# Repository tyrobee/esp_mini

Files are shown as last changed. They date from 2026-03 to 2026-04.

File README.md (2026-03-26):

# esp_mini
A Esp  based flight controller which is really tiny and can be controller through almost everything from your phone to anthor esp and cn also be used as swarn drones likw the drones which do all those cool drone lighting show. Actually i made this drone with that idea only ive been seen those swarn drones show in my school and wated to do smtg like that but there not a single affordable platform for that but you can achevie the same results with this drone at a really affordable range.

## compnents 
- Xiao ESP32 S3 (FC)
- MPU 6050
- 8520 Coreless Motor 2xCW & 2xCCW
- 55mm Propeller 2xCW & 2xCCW
- Coustom motor drive:
    • SI2300 1N-MOSFET 4x
    • 1N4148 Diode 4x
    • 10k ohm Resistor 4X
## Frame
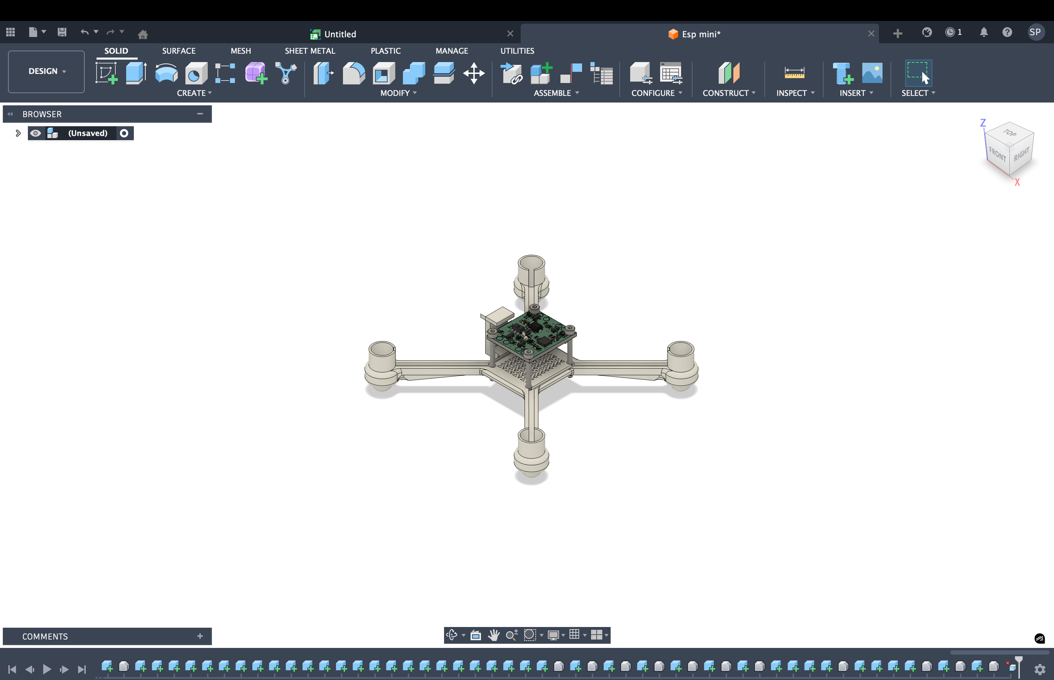
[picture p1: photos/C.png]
C


# Schematics
 Here is the break down of the connections 
  MOTORS-
  M1 --> A8
  M2 --> A3
  M3 --> A2
  M4 --> A0

  MPU6050-
  SDA --> A4
  SCL --> A5

  CRSF- (you can change this part but as i have a csrf radio i have done it for a csrf receiver)
  RX --> D7
  TX --> D6

  3.7v to 5v-
  for reciver to get powered 

  led-
  2 power led
  1 arm led

  Battery Voltage Telemetry-
  Vin --> A1

# PCB 
The PCB is designed in Kicad 
top -
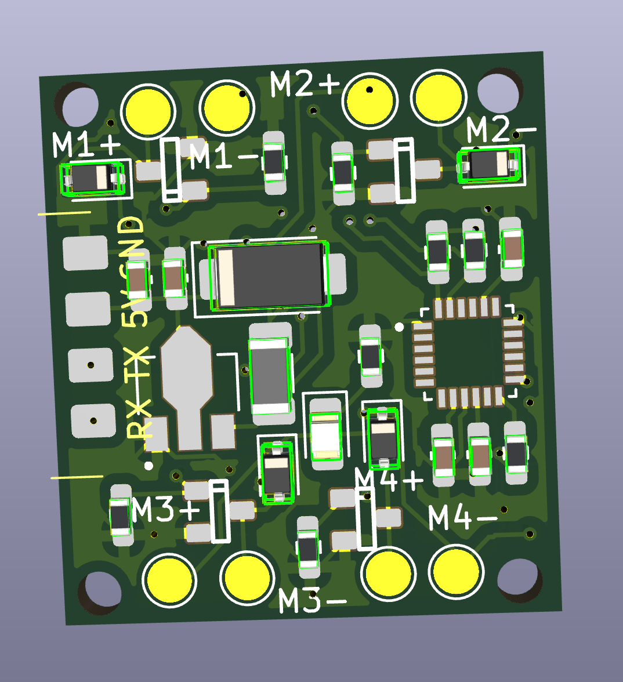
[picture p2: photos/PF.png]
PF


bottom -
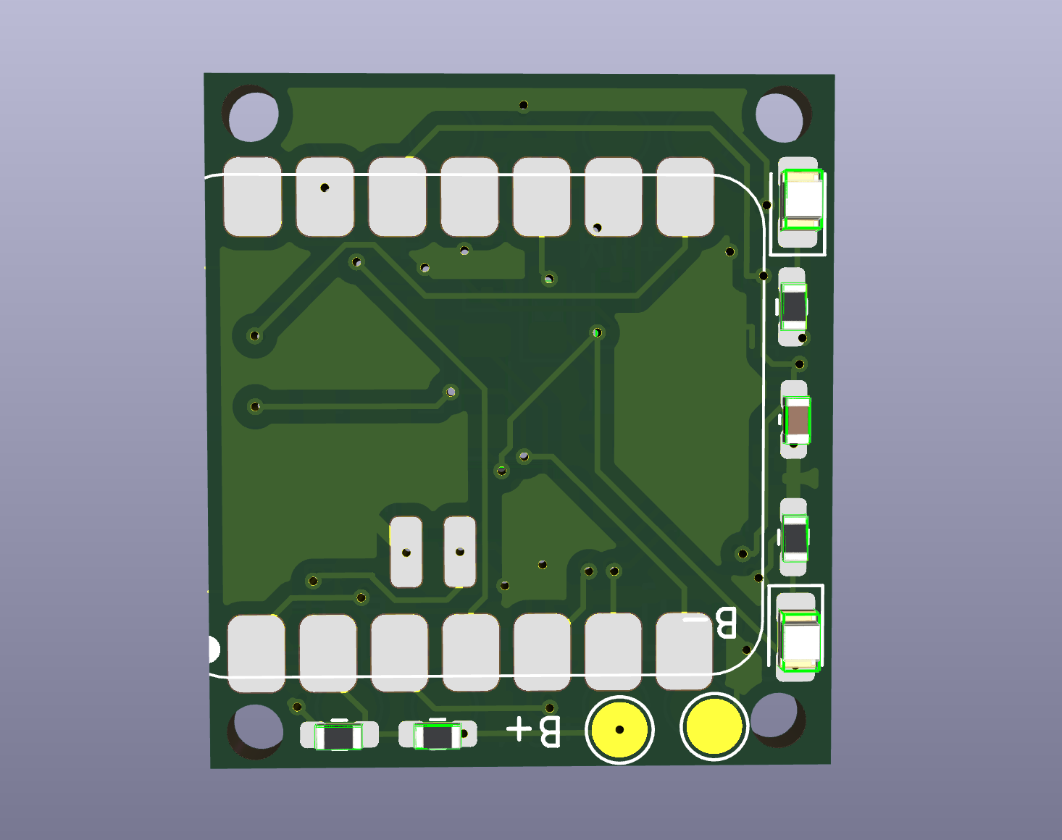
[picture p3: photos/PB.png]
PB


# Firmware

This project uses open-source flight controller firmware from the ESP-FC project,
developed by rtlopez.

- Original firmware repository:
  https://github.com/rtlopez/esp-fc

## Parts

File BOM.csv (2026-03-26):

Item | Description | Quantity | Unit Price($) | Total Price($) | URL
XIAO ESP32 S3 | Flight Controller | 1 | 8.82 | 8.82 | https://robocraze.com/products/seeed-studio-xiao-esp32-s3-development-board-supports-wi-fi-bluetooth-5-0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
8520 Coreless Brushed Motor | Motors | 1 set(4Pcs) | 6.45 | 6.45 | https://roboticsdna.in/product/coreless-motors-720-series-45000-rpm-3-7v/
55 mm Blade Propeller | Propeller | 1set(4Pcs) | 0.56 | 0.56 | https://roboticsdna.in/product/4pcs-set-55mm-white-propeller-for-h107l-h107c-h107d（aperture-1mm）/
1N SI2300 MOSFET | To drive motor | 4 | 0.046 | 0.19 | https://robu.in/product/si2300-hxy-mosfet-20v-6a-350mw-27mω4-5v-500mv-1-n-channel-sot-23-mosfets-rohs/
1N4148 SMD | Diode | 4 | 0.026 | 0.10 | https://robu.in/product/ac1206fr-0710kl-yageo-res-thick-film-1206-10k-ohm-1-0-25w1-4w-±100ppm-c-pad-smd-t-r-automotive-aec-q200/
10k ohm SMD | Resister | 5 | 0.0052 | 0.0262
1k ohm SMD | Resister | 4 | 0.0030 | 0.012
150 ohm SMD | Resister | 3 | 0.0011 | 0.0033
0.01uF SMD | Capacitor | 4 | 0.0030 | 0.012
LED 0805 SMD | Led | 3 | 0.029 | 0.097
ME2108A33P Module | Boost converter | 1 | 0.57 | 0.57 | https://www.flyrobo.in/1.5v-1.8v-2.5v-3v-3.3v-3.7v-4.2v-5v-dc-dc-dc-boost-converter-step-up-module
MPU6050 | Gyro and accelerometer | 1 | 1.91 | 1.91 | https://robu.in/product/mpu-6050-gyro-sensor-2-accelerometer/
1S 300mah battery | Battery | 1 | 1.92 | 1.92 | https://robu.in/product/wly702025-300mah-3-7v-single-cell-rechargeable-lipo-battery/
RadioMaster XR2 Nano | ELRS recover | 1 | 12.12 | 12.12 | https://rcmumbai.com/products/radiomaster-xr2-nano-2-4ghz-expresslrs-receiver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
PCB | Pcb | 5 | 4.9 | 4.9 | SeedStudio
Frame | 3d printing | 1 | 6.4 | 0.9 | 3D
 |  |  | Shipment | 4.56+ 1.66+0.76+0.54+0.65+0.54+1.66 =10.28
 |  |  | Tax(3Dprint & Motors |  | 2.52
 |  |  | Total= | 51.38 ~ 51.5

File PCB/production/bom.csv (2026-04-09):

Designator | Footprint | Quantity | Value | LCSC Part #
B+ | TestPoint_Pad_D2.0mm | 1 | B+
B- | TestPoint_Pad_D2.0mm | 1 | B-
C1, C2, C3, C4 | 0603 | 4 | 0.01uF
C5, C6 | 0603 | 2 | 12uF
D1, D2, D3, D4 | D_SOD-323 | 4 | 1N4148WS
D10 | D_SMA | 1 | SS14
D5, D6, D7 | 0805 | 3 | LED
L1 | 1206 | 1 | 22uH
M1, M2, M3, M4 | SOT23_1_ | 4 | SI2300
M1+ | TestPoint_Pad_D2.0mm | 1 | m1-
M1- | TestPoint_Pad_D2.0mm | 1 | m1+
M2+ | TestPoint_Pad_D2.0mm | 1 | m2+
M2- | TestPoint_Pad_D2.0mm | 1 | m2-
M3+ | TestPoint_Pad_D2.0mm | 1 | m3+
M3- | TestPoint_Pad_D2.0mm | 1 | m3-
M4+ | TestPoint_Pad_D2.0mm | 1 | m4-
M4- | TestPoint_Pad_D2.0mm | 1 | m4+
PS1 | CONV_ME2108A33P | 1 | ME2108A33P
R1, R2, R3, R4 | 0603 | 4 | 1k
R10, R5, R6, R7, R8 | 0603 | 5 | 10k
R11, R12, R9 | 0603 | 3 | 150
U10 | XIAO-ESP32-S3-SMD_PAD | 1 | XIAO-ESP32-S3-SMD
U11 | XR2 NANO | 1 | ~
U3 | QFN50P400X400X95-24N | 1 | MPU-6050

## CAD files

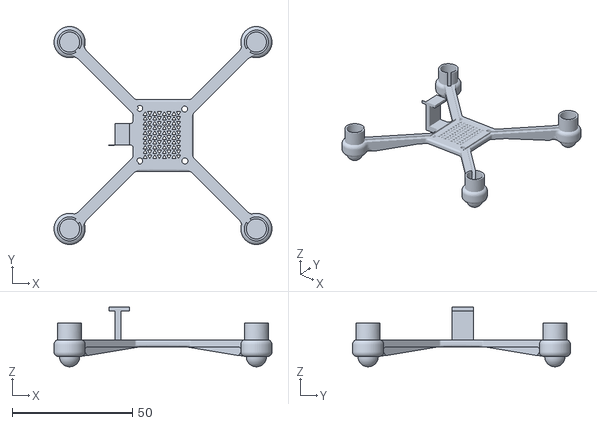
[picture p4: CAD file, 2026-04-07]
esp mini.stl
90.8 x 90.8 x 24.8

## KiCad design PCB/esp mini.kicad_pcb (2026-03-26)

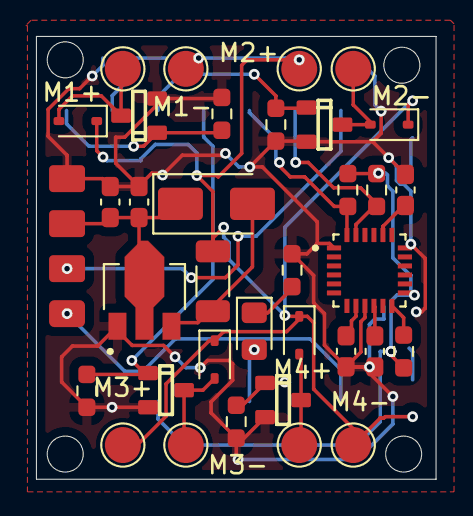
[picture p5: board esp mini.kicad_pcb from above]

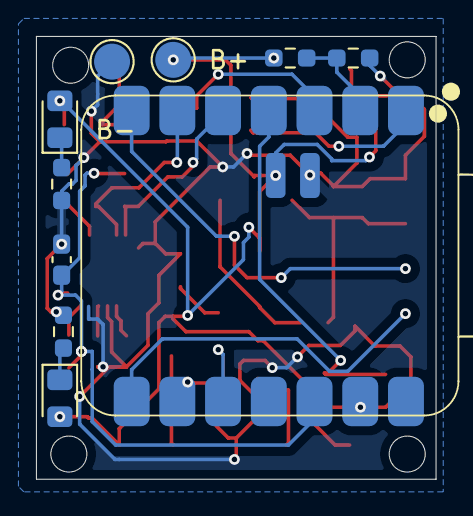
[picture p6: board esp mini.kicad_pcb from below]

Board: 2 copper layers, 22.2 x 24.6 mm, 45 parts (10 on the bottom side), 26 nets.

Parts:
B+: B+; TestPoint_Pad_D2.0mm
B-: B-; TestPoint_Pad_D2.0mm
C1, C2, C3, C4: 0.01uF; C_0603_1608Metric_Pad1.08x0.95mm_HandSolder
C5, C6: 12uF; C_0603_1608Metric_Pad1.08x0.95mm_HandSolder
D1, D2, D3, D4: 1N4148WS; D_SOD-323
D5, D6, D7: LED; LED_0805_2012Metric_Pad1.15x1.40mm_HandSolder
D10: SS14; D_SMA
L1: 22uH; L_1206_3216Metric_Pad1.22x1.90mm_HandSolder
M1, M2, M3, M4: SI2300; SOT23_1_
M1+: m1-; TestPoint_Pad_D2.0mm
M1-: m1+; TestPoint_Pad_D2.0mm
M2+: m2+; TestPoint_Pad_D2.0mm
M2-: m2-; TestPoint_Pad_D2.0mm
M3+: m3+; TestPoint_Pad_D2.0mm
M3-: m3-; TestPoint_Pad_D2.0mm
M4+: m4-; TestPoint_Pad_D2.0mm
M4-: m4+; TestPoint_Pad_D2.0mm
PS1: ME2108A33P; CONV_ME2108A33P
R1, R2, R3, R4: 1k; R_0603_1608Metric_Pad0.98x0.95mm_HandSolder
R5, R6, R7, R8, R10: 10k; R_0603_1608Metric_Pad0.98x0.95mm_HandSolder
R9, R11, R12: 150; R_0603_1608Metric_Pad0.98x0.95mm_HandSolder
U3: MPU-6050; QFN50P400X400X95-24N
U10: XIAO-ESP32-S3-SMD; XIAO-ESP32-S3-SMD_PAD
U11: XR2 NANO

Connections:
+3.3V: C4.1, R5.1, R6.1, R7.1, U3.13 (VDD), U10.12 (3V3)
+3.3VA: B+.1, D1.1 (K), D2.1 (K), D3.1 (K), D4.1 (K), D6.2 (A), D7.2 (A), L1.1, M1-.1, M2+.1, M3+.1, M4-.1, R8.1, U10.15 (BAT)
+5V: C5.1, C6.1, D10.1 (K), PS1.2 (VOUT), U11.3 (5V)
/LBAT: D5.2 (A), U10.10 (PA5_A9_D9_MISO)
/M1: M1.1, R1.2, U10.1 (PA02_A0_D0)
/M2: M2.1, R2.2, U10.3 (PA10_A2_D2)
/M3: M3.1, R3.2, U10.4 (PA11_A3_D3)
/M4: M4.1, R4.2, U10.9 (PA7_A8_D8_SCK)
/RX: U10.8 (PB09_A7_D7_RX), U11.1 (RX)
/SCL: R6.2, U3.23 (SCL), U10.6 (PA9_A5_D5_SCL)
/SDA: R7.2, U3.24 (SDA), U10.5 (PA8_A4_D4_SDA)
/TX: U10.7 (PB08_A6_D6_TX), U11.2 (TX)
/VBAT: R8.2, R10.1, U10.2 (PA4_A1_D1)
/int: R5.2, U3.12 (INT)
GND: B-.1, C1.2, C2.2, C3.2, C4.2, C5.2, C6.2, M1.2, M2.2, M3.2, M4.2, PS1.1 (VSS), R1.1, R2.1, R3.1, R4.1, R9.1, R10.2, R11.2, R12.2, U3.1 (CLKIN), U3.9 (AD0), U3.11 (FSYNC), U3.18 (GND), U10.13 (GND), U10.16 (GND), U11.4 (GND)
unnamed: D1.2 (A), M1.3, M1+.1
unnamed: D2.2 (A), M2.3, M2-.1
unnamed: D3.2 (A), M3.3, M3-.1
unnamed: D4.2 (A), M4.3, M4+.1
unnamed: D5.1 (K), R9.2
unnamed: D6.1 (K), R11.1
unnamed: D7.1 (K), R12.1
unnamed: D10.2 (A), L1.2, PS1.3 (LX)
unnamed: C2.1, U3.20 (CPOUT)
unnamed: C3.1, U3.10 (REGOUT)
unnamed: C1.1, U3.8 (VLOGIC)

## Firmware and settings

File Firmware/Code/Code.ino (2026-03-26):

`#include <WiFi.h>
#include <esp_now.h>
#include <Wire.h>
#include <MPU6050.h>

MPU6050 mpu;


#define M1_PIN 0
#define M2_PIN 2
#define M3_PIN 3
#define M4_PIN 8


#define CH1 0
#define CH2 1
#define CH3 2
#define CH4 3

#define PWM_FREQ 25000
#define PWM_RES 8   


#define MOTOR_MIN 25     
#define MOTOR_MAX 240
#define MOTOR_ARM 15


float kp = 0.18;
float ki = 0.00;
float kd = 0.003;


typedef struct {
  int throttle;
  int roll;
  int pitch;
  int yaw;
  bool armed;
} ControlData;

ControlData rx;


float rollPID, pitchPID, yawPID;
float rollError, pitchError, yawError;
float lastRollErr, lastPitchErr, lastYawErr;


float gx, gy, gz;
unsigned long lastTime;

void onReceive(const esp_now_recv_info_t *info, const uint8_t *data, int len) {
  memcpy(&rx, data, sizeof(rx));
}

void setup() {
  Serial.begin(115200);

  WiFi.mode(WIFI_STA);
  esp_now_init();
  esp_now_register_recv_cb(onReceive);

  
  Wire.begin();
  mpu.initialize();
  mpu.setFullScaleGyroRange(MPU6050_GYRO_FS_1000);

  
  ledcSetup(CH1, PWM_FREQ, PWM_RES);
  ledcSetup(CH2, PWM_FREQ, PWM_RES);
  ledcSetup(CH3, PWM_FREQ, PWM_RES);
  ledcSetup(CH4, PWM_FREQ, PWM_RES);

  ledcAttachPin(M1_PIN, CH1);
  ledcAttachPin(M2_PIN, CH2);
  ledcAttachPin(M3_PIN, CH3);
  ledcAttachPin(M4_PIN, CH4);

  lastTime = micros();
}

void loop() {
  
  if (!rx.armed) {
    stopAllMotors();
    return;
  }


  float dt = (micros() - lastTime) / 1000000.0;
  lastTime = micros();

  
  mpu.getRotation(&gx, &gy, &gz);
  rollRate  = gx / 131.0;
  pitchRate = gy / 131.0;
  yawRate   = gz / 131.0;

  
  rollError  = rx.roll  - rollRate;
  pitchError = rx.pitch - pitchRate;
  yawError   = rx.yaw   - yawRate;

  rollPID  = kp * rollError  + kd * ((rollError  - lastRollErr)  / dt);
  pitchPID = kp * pitchError + kd * ((pitchError - lastPitchErr) / dt);
  yawPID   = kp * yawError   + kd * ((yawError   - lastYawErr)   / dt);

  lastRollErr  = rollError;
  lastPitchErr = pitchError;
  lastYawErr   = yawError;

  int base = map(rx.throttle, 0, 255, MOTOR_MIN, MOTOR_MAX);

  // X quad motor mixing
  int m1 = base + pitchPID + rollPID - yawPID;
  int m2 = base + pitchPID - rollPID + yawPID;
  int m3 = base - pitchPID - rollPID - yawPID;
  int m4 = base - pitchPID + rollPID + yawPID;

  writeMotor(CH1, m1);
  writeMotor(CH2, m2);
  writeMotor(CH3, m3);
  writeMotor(CH4, m4);
}

void writeMotor(int ch, int val) {
  val = constrain(val, MOTOR_ARM, MOTOR_MAX);
  ledcWrite(ch, val);
}

void stopAllMotors() {
  ledcWrite(CH1, 0);
  ledcWrite(CH2, 0);
  ledcWrite(CH3, 0);
  ledcWrite(CH4, 0);
}
